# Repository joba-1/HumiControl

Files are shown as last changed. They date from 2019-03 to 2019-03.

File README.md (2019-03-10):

# Humidity Control

## Current Status

* A Bosch BME280 delivers air humidity data
* An analog capacitive moisture sensor delivers soil humidity data
* A fan is controlled with a pwm pin via web slider control or flash button
* Automatic mode uses humidity value to set fan speed.
* Setup wifi with captive portal.
* Reset wifi settings with long press of flash button
* Led feedback:
    * fast blink: boot setup and wifi connect
    * slow blink: wifi setup
    * on: normal operation
    * off: flash button pressed (on again if long press detected)

## Todo

* mDNS does not work properly
* mqtt integration
* configurable limits for the automatic fan control

## Flash Software Installation

Precondition: Python V2

### PlatformIO

    pip install platformio

### Arduino Framework for PlatformIO

    pio platforms install espressif8266 --with-package framework-arduinoespressif8266

## Wiring

If you want to use other pins, adjust the #defines accordingly.

### BME280

This is a breadboard friendly wiring for a standard BME280 breakout board and a NodeMCU:
All pins align, no extra wiring necessary.

    BME280 GND <--> ESP8266 GND
    BME280 SCL <--> ESP8266 D5 (D1 is standard)
    BME280 SDA <--> ESP8266 D6 (D2 is standard)
    BME280 3V3 <--> ESP8266 3V3

### Capacitive Soil Moisture Sensor (V1.2)

    CAP GND  <--> ESP8266 GND
    CAP VCC  <--> ESP8266 3V3
    CAP AOUT <--> ESP8266 A0

### Fan Power

    for PWM control of a fan connect D5 with mosfet gate.
    Schematics and pcb board are in the eagle/ subfolder (warning: uses rare p-channel mosfet).

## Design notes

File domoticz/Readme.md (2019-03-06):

# Example lua script to read json sensor values

* Put the script in /opt/domoticz/scripts/lua_parsers
* Create domoticz hardware device "HTTP/HTTPS poller"
    * use http://192.168.1.139/json for the url (replace 192.168.1.139 with your sensors ip or hostname)
    * As content type use application/json
    * As command use the lua script filename
* Create domoticz devices by selecting "create virtual sensor"
    * use custom type or temp/humi/baro
* Edit the script to replace the domoticz id's with those just created

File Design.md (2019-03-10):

# HumidityControl

* Wlan manager for ip config. Async possible?
    * See https://github.com/tzapu/WiFiManager/issues/723
* Measure humidity
    * if no humidity device, scan i2c for bme280 or bmp280
    * if device, read temperature, humidity, pressure if available
* Control fan via mqtt:
    * Always on
    * Always off
    * Automatic
        * Switch on fan if humidity is above maximum
        * Switch off fan if humidity is below minimum
        * In between set fan speed according to humidity
* If new temperature/hum/press/fan status, then publish to mqtt
* Device configuration via mqtt
    * Set device name (replace {nx} or {nd} with n hex or dec digits of device id)
    * Set mqtt topic template (replace {n} with device name and {t} for subtopic)
        * Fallback humi/{6x}/{t} is always valid
    * Reset wlan config and reboot to activate wlan manager
    * Set maximum humidity (turns on fan)
    * Set minimum humidity (turns off fan)
    * Set fan speed percent if always on
    * Set led brightness percent
* Device query via mqtt
    * ip
    * name
    * version
    * topic template
    * uptime
    * temperature/humidity/pressure
    * fan mode
    * fan power status
    * humidity maximum
    * humidity minimum
    * percent fan usage in automatic mode
    * led brightness percent
    * fan rpm
    * all
* Button toggles on/off/auto, multiple: Set wlan manager status, long: reboot
* ws2812 or rgb led yellow = below minimum humidity ... blue = above maximum humidity
* ws2812 or rgb led red = always off, white = always on

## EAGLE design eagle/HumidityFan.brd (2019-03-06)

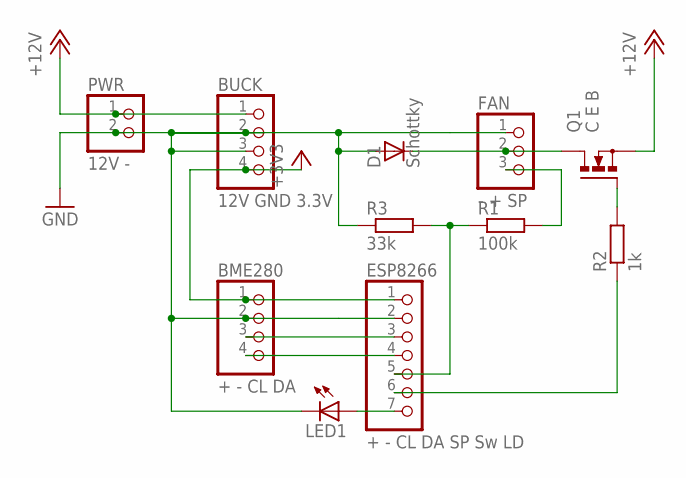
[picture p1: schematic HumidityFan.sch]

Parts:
BME280: + - CL DA; 1X04
BUCK: 12V GND 3.3V; 1X04
D1: Schottky; DO35-10
ESP8266: + - CL DA SP Sw LD; 1X07
FAN: - + SP; 1X03
LED1: LED5MM
PWR: 12V -; 1X02
Q1: C E B; TO220BV
R1: 100k; 0204/7
R2: 1k; 0204/7
R3: 33k; 0204/7

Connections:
+3V3: BME280.1, BUCK.4, ESP8266.1
+12V: BUCK.1, PWR.1, Q1.S
GND: BME280.2, BUCK.2, BUCK.3, D1.A, ESP8266.2, FAN.1, LED1.K (C), PWR.2, R3.1
unnamed: Q1.G, R2.2
unnamed: D1.C, FAN.2, Q1.D
unnamed: ESP8266.6, R2.1
unnamed: ESP8266.7, LED1.A
SCL: BME280.3, ESP8266.3
SDA: BME280.4, ESP8266.4
SPD3.3V: ESP8266.5, R1.1, R3.2
SPD12V: FAN.3, R1.2

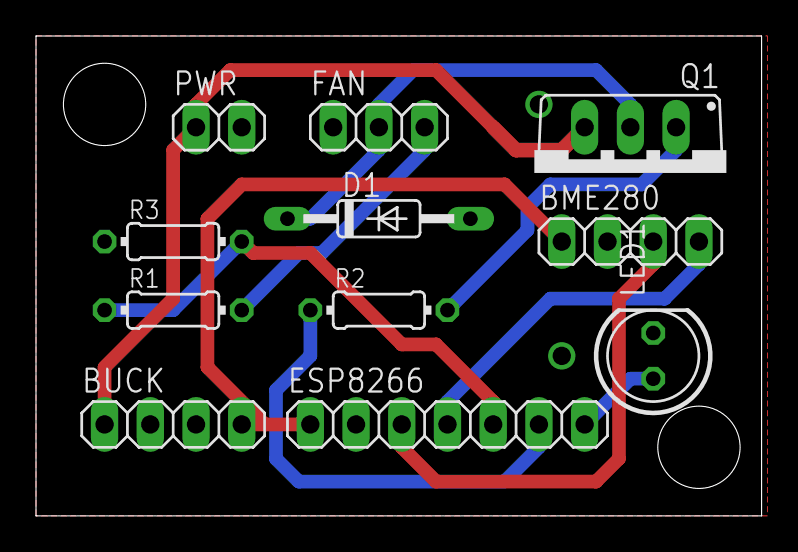
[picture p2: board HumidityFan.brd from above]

Board: 2 copper layers, 40.3 x 26.7 mm, 11 parts (0 on the bottom side), 11 nets.

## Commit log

2019-03-03 Humidity Control - measure humidity and control a fan
2019-03-03 added bme280 lib, switched to OTA
2019-03-04 Use other pins to better line up with the connector. Use external LED for feedback. Fan control with web page buttons and physical (flash) button short press (long press is still wlan config reset)
2019-03-04 add fan speed control
2019-03-05 better pwm fan speed handling
2019-03-06 add eagle pcb
    [HumidityFan.brd, HumidityFan.sch]
2019-03-06 switch fan on and off button
2019-03-06 add domoticz lua parser for this sensor
2019-03-10 automatic humidity driven fan speed
2019-03-10 persistent setting for automatic fan speed flag (default is off)
2019-03-10 button press toggles fan off -> on -> auto -> off
2019-03-10 update speed after toggle to automatic fan control
